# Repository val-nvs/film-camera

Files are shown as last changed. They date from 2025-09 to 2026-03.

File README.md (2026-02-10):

# 3D Printed Clawless 35mm Film Camera

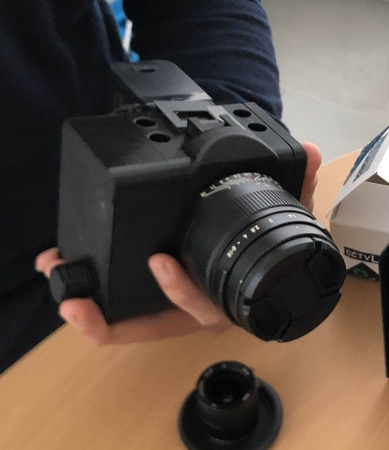
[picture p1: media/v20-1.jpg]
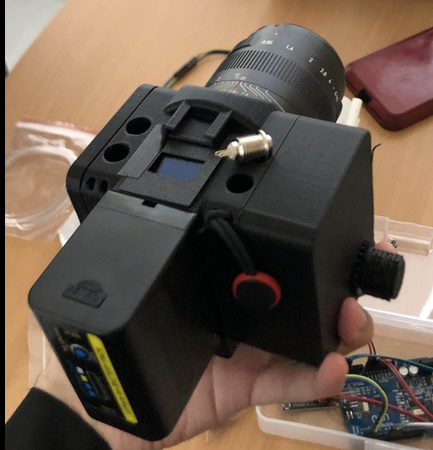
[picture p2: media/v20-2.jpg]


This repository documents the build of a 3D printed film camera that is designed to use standard 35mm 36exp film cartridges. With the goal of shooting small clips on a budget. By **[Valdir Neves](https://www.instagram.com/val.nevs/)** & **[Charlie Chaves](https://www.instagram.com/charliechavess/)**.

[{{{ **View in 3D on onshape** }}}](https://cad.onshape.com/documents/5c2b9c47264034ac5c1a5ddc/w/cf712b211e6f3dfb560adac5/e/ec23c9e4d3ee5216bc6ef26c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)

## Acknowledgements

Thanks to **[Hans Boden](https://github.com/hans-boden)** for guidance and support throughout this project, including lending a 3D printer.

Thanks to [MILL - Makers In Little Lisbon](https://www.instagram.com/lxmill/) for providing a platform for connecting with other makers.

Thanks to [Elly T.](https://www.instagram.com/forfutureelly/) and [Daniel @photonbit](https://www.instagram.com/photonbit/) for design advice.

## Inspiration

- Joshua Bird https://joshuabird.com/blog/post/3d-printed-film-video-camera
	
	
- Blaž Semprimožnik https://blazsemprimoznik.com/okto35-mk3
	
	
- Brian's Lucky Box Camera
	
	
- henry kidman
	
	
	

## About:

3D printed film camera, designed to use standard 35mm 36exp film. Capable of taking photos and making 1 to 4 short clips per roll.

Goals:

- To be a low cost-of-entry into analog motion picture with easily accesible film and labs. ~11€ film + ~15€ developing. (Super 8 starts at 23€+ B&W, color at 50€+, and it's harder to find somewhere to develop).

- To be low cost when bulk loading (when someone rolls their own 5ft rolls from a 100ft or 400ft spool). I'm using Lucky SHD50 B&W bulk loaded- 1.9€ per roll. Fomapan would be around 2.7€ per roll when bulk loaded.

Highlights:

- 2 Motors: Instead of a single motor with a system of gears to connect the shutter and pulldown mechanism, the mechanisms are independent of each other by using a motor for each.

- Clawless: Instead of claws to pulldown the film by the perforations, it simply winds the film into the camera with sticky tape. Possible due to the short total lenght of the film strip (150cm instead of 30m or 120m). Pros: simpler; frame can be any height/aspect ratio. Downside: almost impossible to project videos- must be scanned digitally.

- Multitrack video-recording: Possible to record up to 4 separate discrete tracks of video (not simultaneously) by shifting the internal assembly (and rewinding) after finishing each track. Comes with 4 options of gates to record between 1 to 4 tracks, with more options for taller aspect ratios like 1:1.

- Maximum FPS for video: ???

- Records 1600 frames per canister with the smallest gate (divided into 4 passes) (2min@13fps). Or 820 frames using a "Super 16" sized gate (divided into 2 passes), at 24fps it would be 34s of total recording time- 45s@18fps 1min@14fps.

Features:

- E-mount used, easy to adapt to many lenses And it's easier to print compared to C-mount- with it's fine threads.

- With the smallest "Super 8" gate you can film up to 1200 frames per cartridge (divided into 4 passes).

Future plans:

- OLED screen tracks how much film you used.
- Unique manual variable FPS feature designed to [save on film] or [add slow motion] mid-shoot. (Each frame will be logged in time making it easy to sync frames and sound).

## 3D model
[{{{ **View in 3D on onshape** }}}](https://cad.onshape.com/documents/5c2b9c47264034ac5c1a5ddc/w/cf712b211e6f3dfb560adac5/e/ec23c9e4d3ee5216bc6ef26c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)

## Code
[Wokwi](https://wokwi.com/projects/455248968650449921)

## Setup

- Onshape CAD software on Chrome
- UltiMaker Cura 5.11.0 Slicer
- Anycubic i3 Mega S Printer / 0.4mm nozzle / SMARTFIL 1.75mm Black PLA

## Parts

Motors:

- 1x Nema 8 Stepper Motor for the shutter 
- 1x Nema 14 Stepper Motor to pull film 

Other parts:

- 2x Stepper Driver DRV8825 
- Arduino and breadboard ~15€
- 2x Tripod threaded insert (1/4") length 6mm 
- Optional: 8x 5x3mm round magnets 
- 4x Buttons: 

Viewfinder:

- Acrylic lens 24.8mm diameter 
- Front surface mirror 30x30x2mm 
- Plastic Fresnel lens f=28mm 30x30mm 

Lens:

- Lens mount adaptor C-NEX (to support C-mount lenses) 
- Lens: 3.6-10mm f/1.4 C-Mount [1/1.8"] "8MP IR CCTV" (effectively f/2) 
- Optional: Imaging lens cover 

## 3D Printed parts (v21)

- Body
- Core
- Left and right wall
- Shutter disc
- Rewinder pin
- Optional: 2 gears and 2 locking pins

## History

Feb 10 - test failed, not enough force to pull film consistently

Feb 9 - test failed, solder fail

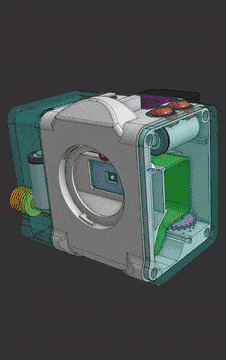
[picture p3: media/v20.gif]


v21 - TBA
```
- smaller body, eletronics outside
- integrated viewfinder into body
```

v20b - Jan 19, 2026
```
- shave off parts of gate and oled lid
- added lock pin
- supressed NPF wiring ducts
- fix shutter piece
- fix roller size
- rotate mount slightly
- widen button holes
```
v20a - Jan 9, 2026
```
- added support for roller on core
```
v20 - Jan 1, 2026
```
- FDM focused redesign
- better gears
- add 4 magnets on each wall
```

v19 - Nov 25, 2025
```
v19a: added switches - Nov 26, 2025
```
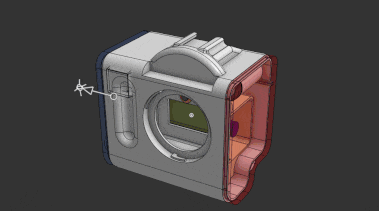
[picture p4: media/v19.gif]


v18
```
- Not symmetric
- Custom buttons
```

v17

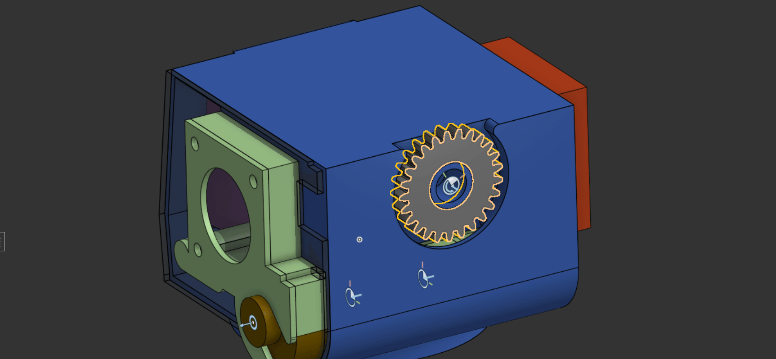
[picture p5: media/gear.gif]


```
- Gear to move core
- 2x RCR123A
- OLED
```

v16
```
- Protuding shutter design thing
```

v15
```
- Fixed wrong flange value!
- Core completely encased to prevent light leaks
- Core on bottom
- Nema 8 for film
- Nema 14 for shutter
- Cold Shoe
```

v14
```
- Nema 8 for film
- 0530 6V Solenoid for shutter
- 2x RCR123A
```

v13
```
- Tests with solenoid for shutter and shifted reel motor
```

v12 - PRINTED @JLC3DP - July 31, 2025

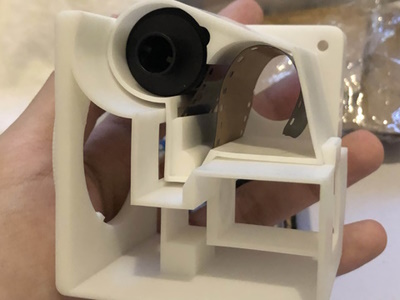
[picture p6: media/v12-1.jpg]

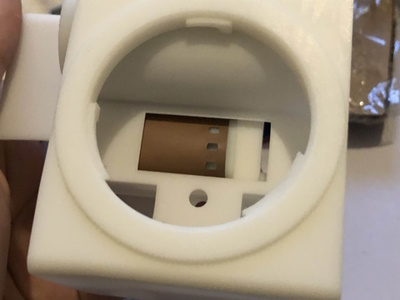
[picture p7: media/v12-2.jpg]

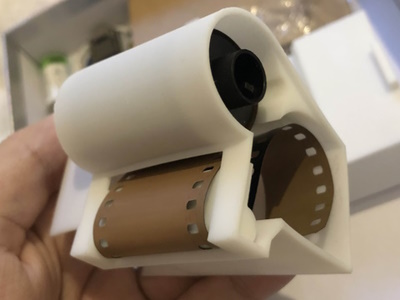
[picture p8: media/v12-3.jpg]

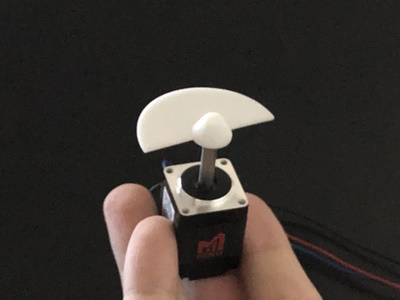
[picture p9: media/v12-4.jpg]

```
- Wrong flange value!
- Nema 14 for film 
- Nema 8 for shutter
- 71x72x67mm
- 2x RCR123A batteries and holder https://www.takachi-enclosure.com/assets/attachments/images/CR123A-PC.pdf
```


v11
```
- 4x RCR123A batteries
```

v10
```
?
```

v9


```
- Uses separate motors for each function instead of complex gears. One motor spins the shutter disc, another advances the film.
- Nema 17 for film and shutter
- 4x AAAA batteries
```

# Film scanner
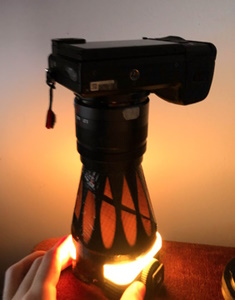
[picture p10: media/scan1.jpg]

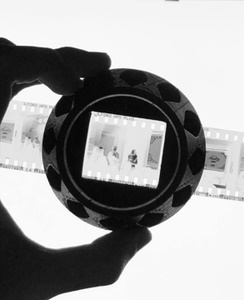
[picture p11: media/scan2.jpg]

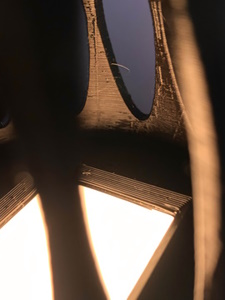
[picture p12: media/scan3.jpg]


to photo scam 35mm 8 perforations film
using 7artisans 35mm f/.95 and a small video light (NEEWER RGB61 iirc)

- v3 printed but film gets jammed
- v6 works great, 2 identical pieces that connect each-other for the base, and one tube piece to hold the lens. easy to adapt other lenses with .step file
- v7 will add phone holder to use the flashlight to see dust particles on top of the film like the laser dyson vacuum

# etc

```
38exp = 1444mm
100ft = 30480mm
24.9 width
16:9 ratio
0.05 gaps between
@ 24 fps
```

```
@ 2 columns (12.42x6.989) (86.8mm²) (7.039mm pitch)
 38 exp: 17 sec
 100 ft: 6    min
 400 ft: 24   min
1000 ft: 60.1 min
```

```
@ 3 columns (8.26x4.65) (38.4mm²) (4.700mm pitch)
- ` 38 exp`: 38.4 sec
- ` 100 ft`: 13.5  min
- ` 400 ft`: 54    min
- `1000 ft`: 135.1 min
```

```
@ 4 columns (6.187x3.48) (21.5mm²) (3.530mm pitch)
-  38 exp: 68.1 sec
-  100 ft: 23.98 min
-  400 ft: 95.92 min
- 1000 ft: 239.8 min
```

```
- Super 16 @ 16:9 crop = 88.22 mm²
- 16mm     @ 16:9 crop = 59.24 mm²
- Super 8  @ 16:9 crop = 18.87 mm²
- 8mm      @ 16:9 crop = 11.39 mm²
```

# etc
Tripod threaded insert (1/4") length 6mm

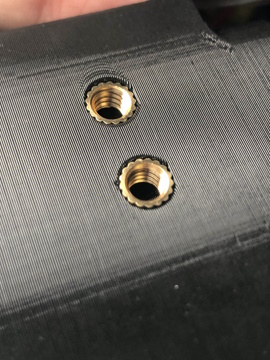
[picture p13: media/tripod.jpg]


100ft of film makes 20 "36exp" cartridges

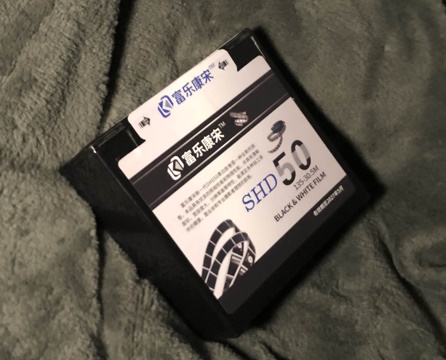
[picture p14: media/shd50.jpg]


6.3-10mm f/1.4 C-mount lens

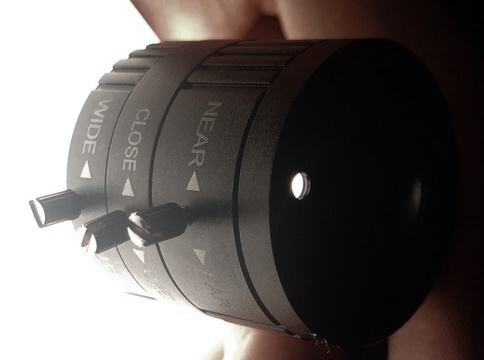
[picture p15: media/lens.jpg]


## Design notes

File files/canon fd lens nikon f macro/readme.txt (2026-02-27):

size of piece =/= macro size, due to flange difference.
macro cant go lower than around 16.5mm, due to flange difference.

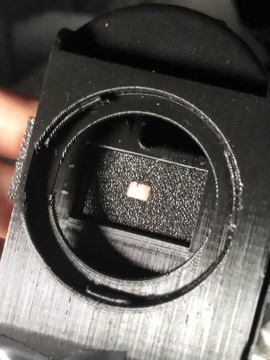
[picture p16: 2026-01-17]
media/gate.jpg

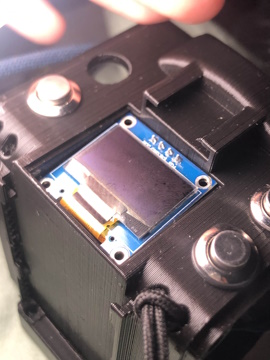
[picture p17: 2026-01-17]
media/v20-3.jpg

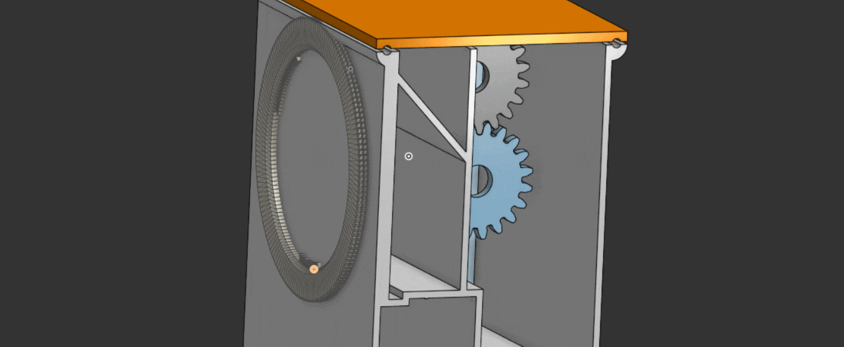
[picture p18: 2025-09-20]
media/v13.gif

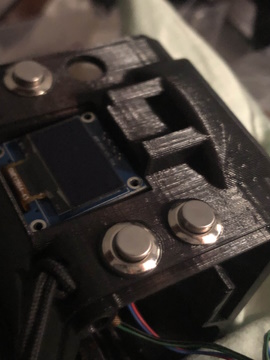
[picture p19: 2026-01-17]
media/v20-4.jpg

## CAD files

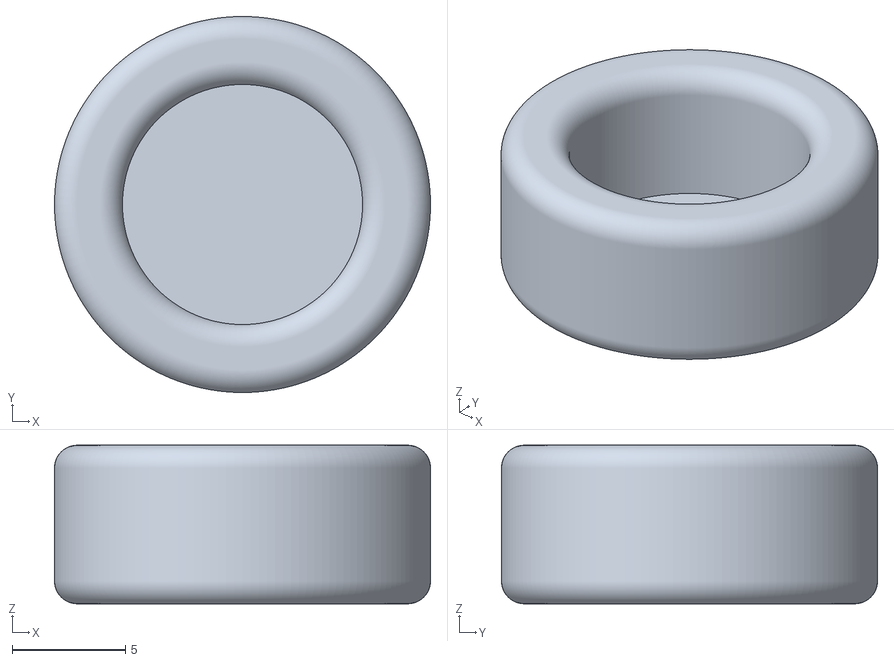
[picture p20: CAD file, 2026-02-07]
files/c-rear-element-cap.stl
16.6 x 16.6 x 7.00

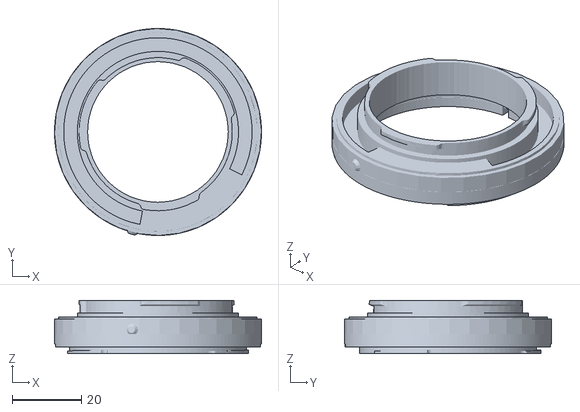
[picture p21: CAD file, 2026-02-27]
files/canon fd lens nikon f macro/FD-Lens on Nikon-F macro 20mm.stl
60.0 x 60.0 x 15.5

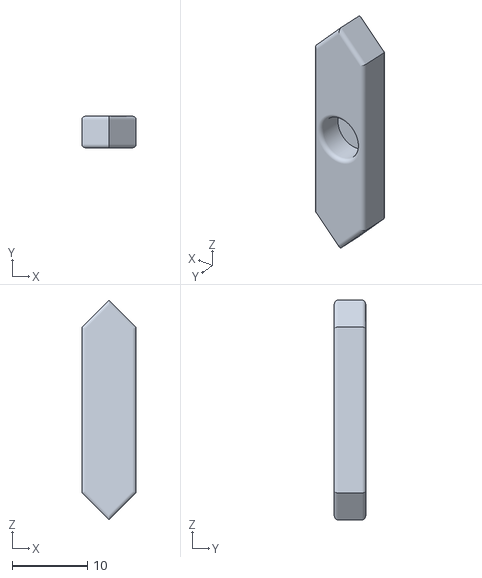
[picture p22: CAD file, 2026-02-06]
files/clapper/clapper v1/clapper v1 - segment x30.stl
7.20 x 4.20 x 29.2

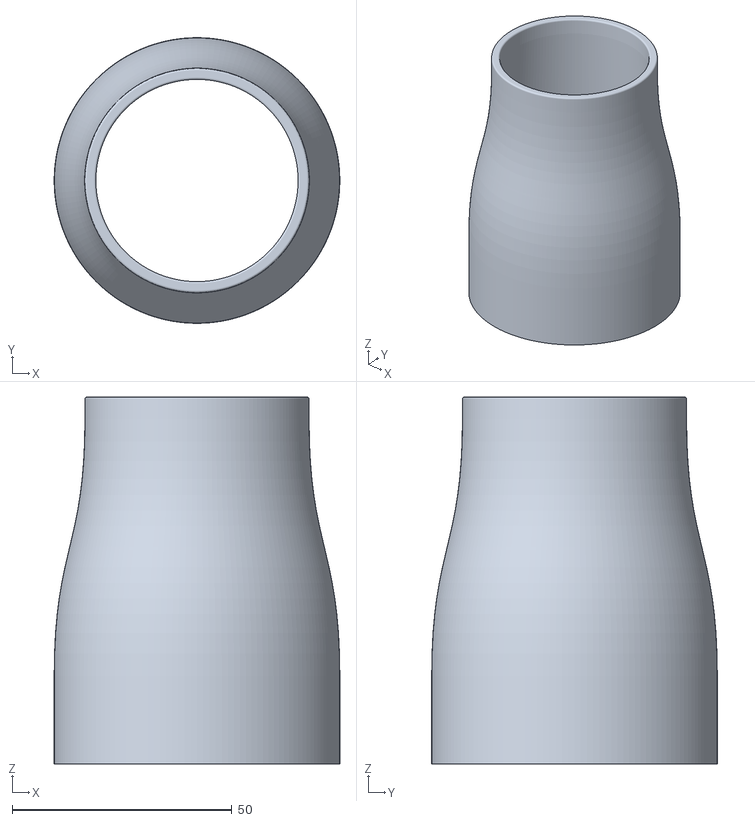
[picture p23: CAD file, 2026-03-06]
files/film scanner/scan v7/new/scan v7 test 2 - tube 90mm.stl
65.0 x 65.0 x 83.5

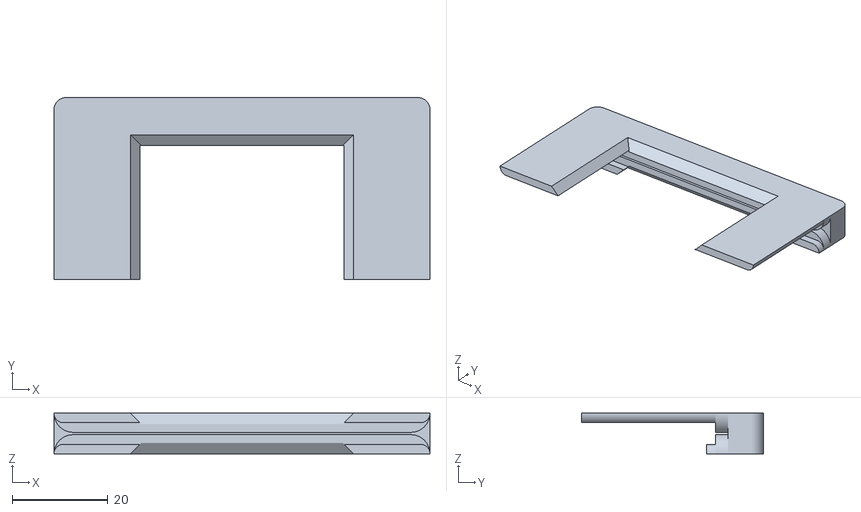
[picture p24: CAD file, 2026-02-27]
files/film scanner/scan v7/scan v7 - holder x2.stl
78.4 x 37.9 x 8.50

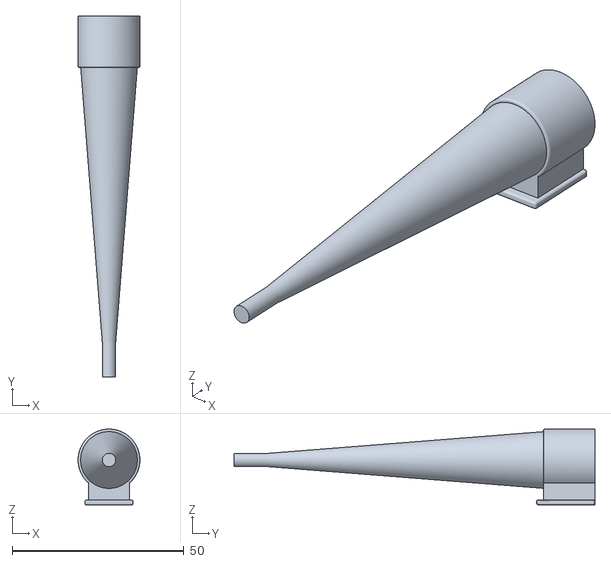
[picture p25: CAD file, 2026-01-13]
files/filter spin/filter spin 72mm - Part 3.stl
18.0 x 105.0 x 22.1

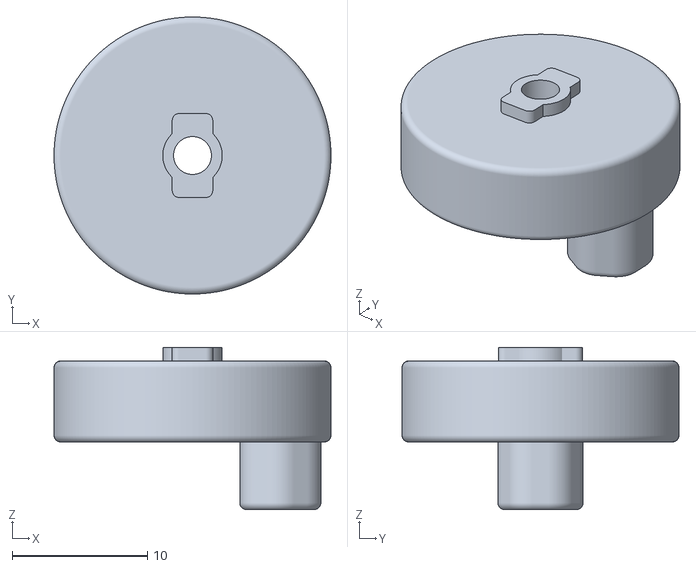
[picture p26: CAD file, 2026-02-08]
files/p30t rewinder/p30t rewinder - v2.stl
20.5 x 20.5 x 12.0

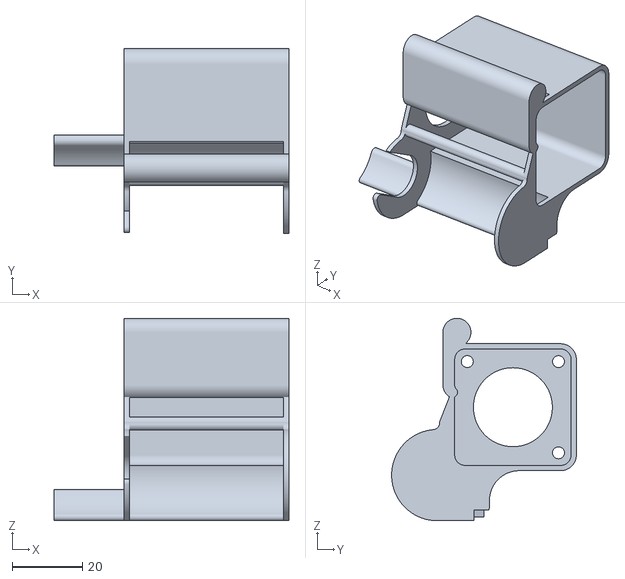
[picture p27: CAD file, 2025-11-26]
files/v19a/v19a - core.stl
67.0 x 52.7 x 57.7

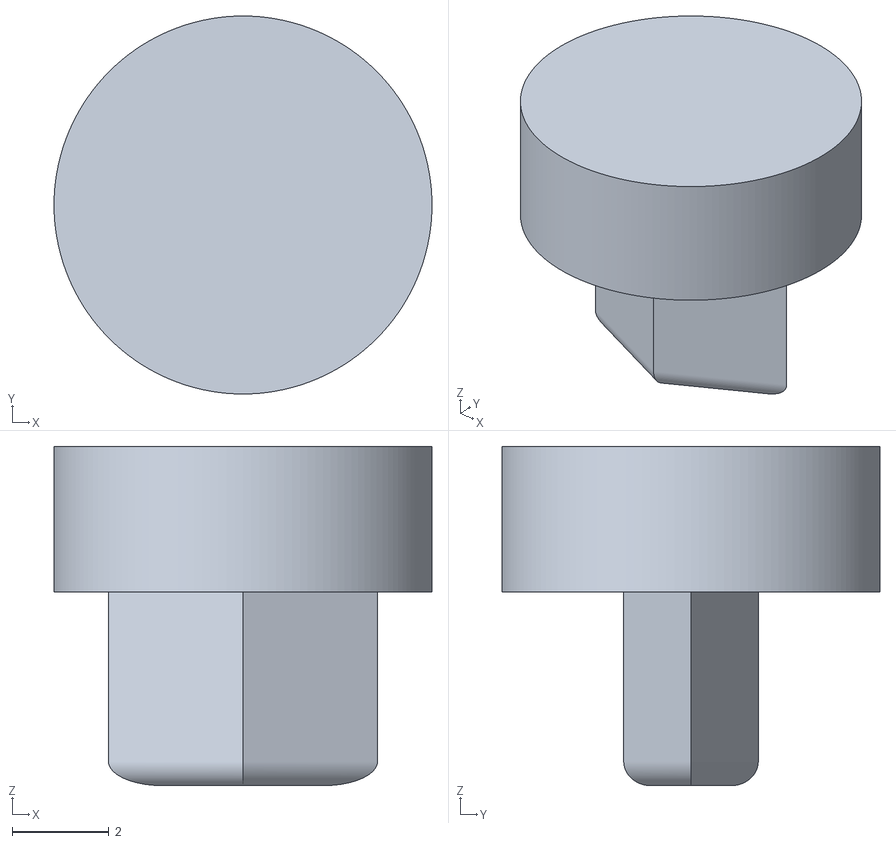
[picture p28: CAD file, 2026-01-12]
files/v20a/v20a - gear pin x3 new.stl
7.80 x 7.80 x 7.00

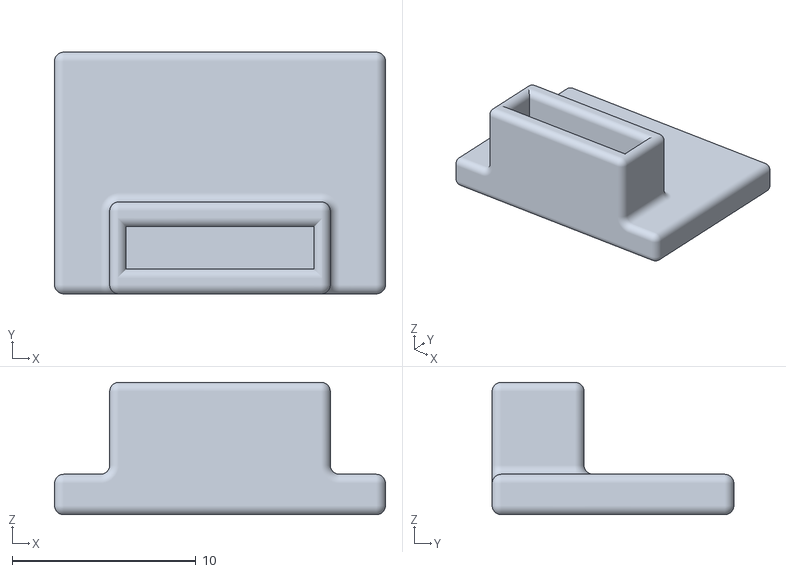
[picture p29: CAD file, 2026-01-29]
files/v20b/v20b - viewfinder part B.stl
18.0 x 13.1 x 7.20

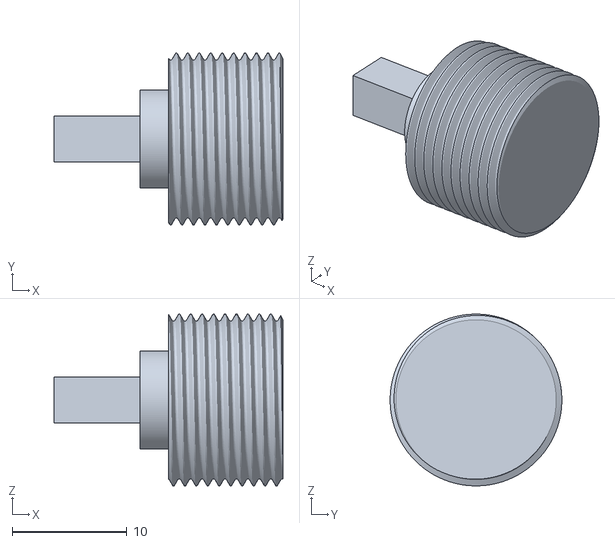
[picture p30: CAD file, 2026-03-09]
files/v24/v24 - worm knob.stl
20.0 x 15.0 x 15.0

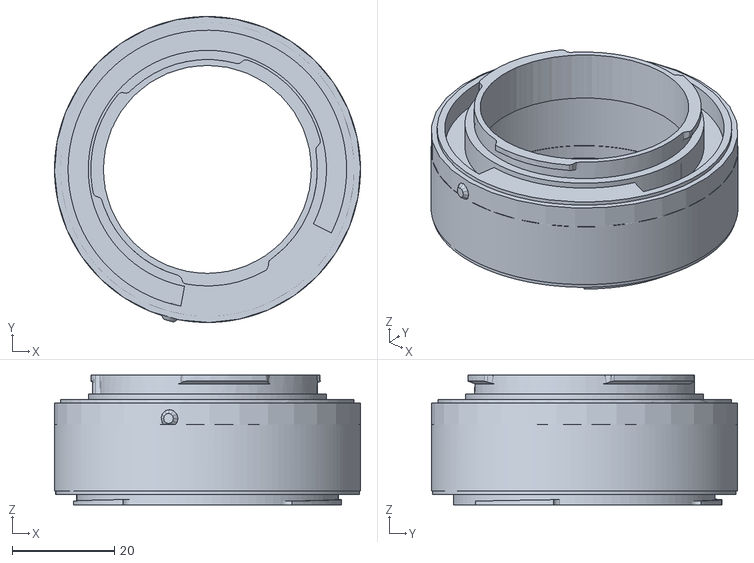
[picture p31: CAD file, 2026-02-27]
files/canon fd lens nikon f macro/FD-Lens on Nikon-F macro 30mm.stl
60.0 x 60.0 x 25.5

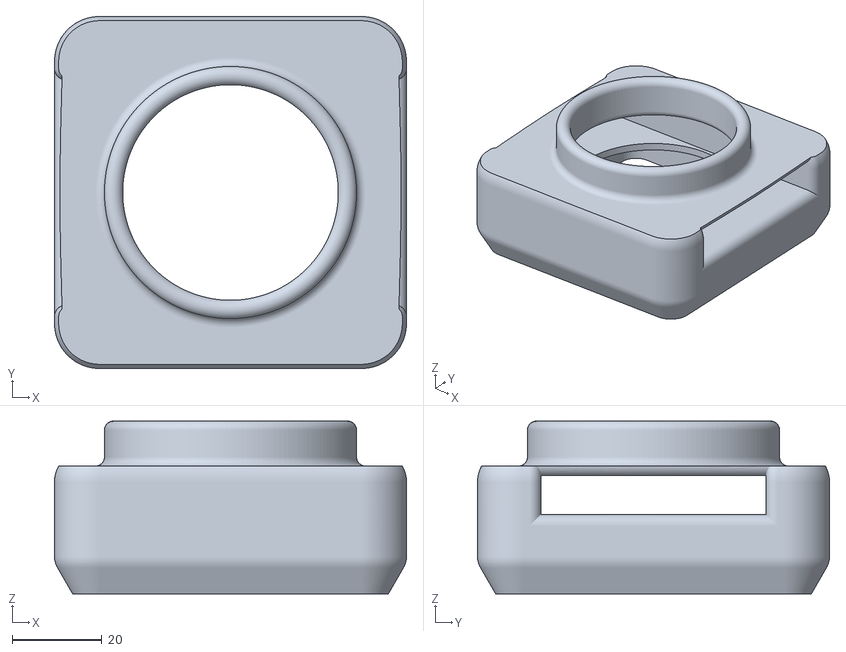
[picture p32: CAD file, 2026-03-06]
files/film scanner/scan v7/new/scan v7 test 2 - base.stl
78.4 x 78.4 x 38.5

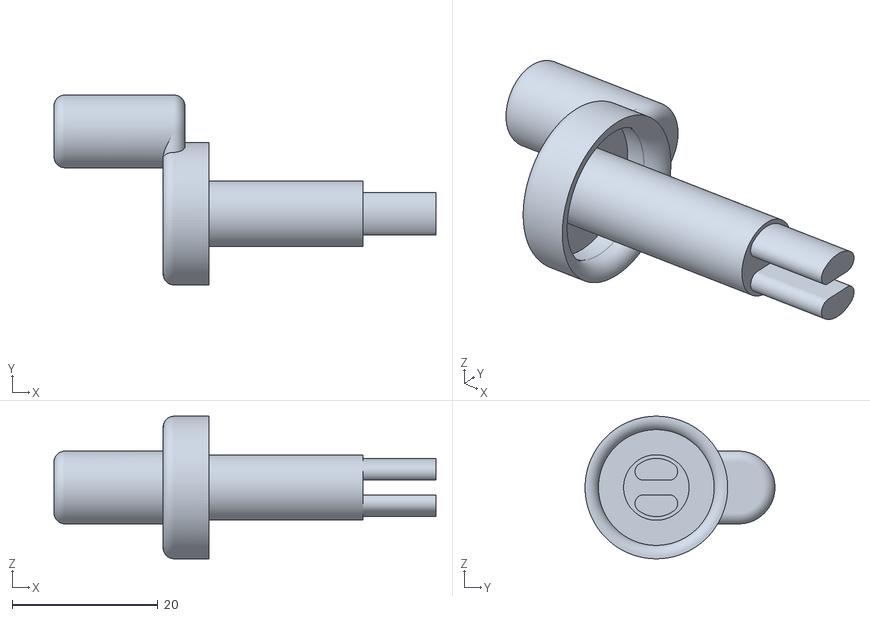
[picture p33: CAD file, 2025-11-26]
files/v19a/v19a - rewinder.stl
52.5 x 26.1 x 19.6

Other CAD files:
files/v20a/v20a - gear pin x3.stl
files/v20b/v20b - shutter.stl
files/v24/v24 - wall right.stl
files/canon fd lens nikon f macro/FD-Lens on Nikon-F macro 17mm.stl
files/canon fd lens nikon f macro/FD-Lens on Nikon-F macro 25mm.stl
files/film scanner/scan v1/scan v1 test.stl
files/film scanner/scan v1/scan v1.stl
files/film scanner/scan v2/scan v2.stl
files/film scanner/scan v3/scan v3.stl
files/film scanner/scan v4/scan v4 - base x2.stl
files/film scanner/scan v4/scan v4 - tube.stl
files/film scanner/scan v6/scan v6 - tube for 7artisans35mmf095+macro16mm.stl
files/film scanner/scan v7/new/scan v7 test 2 - base (1).stl
files/p30t rewinder/p30t rewinder - v1.stl
files/v12/v12 - core.stl
files/v12/v12 - gate 1250x700.stl
files/v12/v12 - gate 625x352.stl
files/v12/v12 - gate 833x469.stl
files/v12/v12 - lid.stl
files/v12/v12 - shutter.stl
files/v12/v12 - spool flat.stl
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

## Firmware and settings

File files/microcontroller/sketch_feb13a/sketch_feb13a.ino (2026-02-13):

#include <LedControl.h>

// ===== ARDUINO R4 WIFI BUILT-IN MATRIX - START =====
#include "Arduino_LED_Matrix.h"
// ===== ARDUINO R4 WIFI BUILT-IN MATRIX - END =====

// MAX7219 Pins: DIN=12, CLK=13, CS=A0
LedControl lc = LedControl(12, 13, A0, 2);  // 2 displays chained

// ===== ARDUINO R4 WIFI BUILT-IN MATRIX - START =====
// Built-in R4 WiFi LED Matrix
ArduinoLEDMatrix matrix;
// ===== ARDUINO R4 WIFI BUILT-IN MATRIX - END =====

// Motor Pins
const int en1 = 2, step1 = 3, dir1 = 4;
const int en2 = 5, step2 = 6, dir2 = 7;

// D-pad Buttons
const int btnDown = 8;
const int btnRight = 9;
const int btnUp = 10;
const int btnLeft = 11;

// Menu state
int currentMenu = 0;  // 0 = main menu, 1 = submenu shutter, 2 = submenu claw, 3 = shutter speed submenu, 4 = both submenu, 5 = fps submenu, 6 = duration submenu
int selectedLine = 0; // 0 = top line (motor1), 1 = middle line (motor2), 2 = bottom line (both)
int shutterSubSelection = 0; // 0 = lock, 1 = run shutter, 2 = speed settings, 3 = unused
int clawSubSelection = 0; // 0 = lock, 1 = run claw, 2 = skip, 3 = unused
int bothSubSelection = 0; // 0 = lock/unlock both, 1 = run, 2 = fps, 3 = duration
bool motor1Locked = false; // Motor 1 (shutter) lock state
bool motor2Locked = false; // Motor 2 (claw) lock state

// FPS settings for Both menu
const float fpsValues[] = {60.0, 48.0, 30.0, 24.0, 20.0, 18.0, 15.0, 12.0, 10.0, 9.0, 8.0, 6.0, 5.0, 4.0, 3.0, 2.0, 1.5}; // Frames per second
const int numFPS = 17;
int fpsIndex = 12; // Default to 5 FPS

// Duration (cycles) settings for Both menu
const int cyclesValues[] = {1, 5, 10, 20}; // Number of cycles
const int numCycles = 4;
int cyclesIndex = 0; // Default to 1 cycle

// Shutter speed array in microseconds: .1 .15 .2 .3 .4 .5 1 2 3 4 5 8 10 16 25 32 50 60 120 180
const long speedValues[] = {
  100000,    // .1
  150000,    // .15
  200000,    // .2
  300000,    // .3
  400000,    // .4
  500000,    // .5
  1000000,   // 1
  2000000,   // 2
  3000000,   // 3
  4000000,   // 4
  5000000,   // 5
  8000000,   // 8
  10000000,  // 10
  16000000,  // 16
  25000000,  // 25
  32000000,  // 32
  50000000,  // 50
  60000000,  // 60
  120000000, // 120
  180000000  // 180
};
const int numSpeeds = 20;
int speedIndex = 5; // Default to .5s (index 5)

unsigned long lastBlink = 0;
bool blinkState = false;

uint8_t frame[8][12] = {0};  // Only using 12x8 space

void setup() {
  // ===== ARDUINO R4 WIFI BUILT-IN MATRIX - START =====
  // Initialize built-in R4 WiFi LED matrix
  matrix.begin();
  // ===== ARDUINO R4 WIFI BUILT-IN MATRIX - END =====
  
  // Initialize both MAX7219 displays
  delay(50);  // Small delay before init
  lc.shutdown(0, false);  // Wake up display 0
  lc.shutdown(1, false);  // Wake up display 1
  lc.setIntensity(0, 8);  // Set brightness (0-15)
  lc.setIntensity(1, 8);
  lc.clearDisplay(0);
  lc.clearDisplay(1);
  delay(50);  // Small delay after init
  
  int outputs[] = {en1, step1, dir1, en2, step2, dir2};
  for(int p : outputs) pinMode(p, OUTPUT);
  
  int inputs[] = {btnDown, btnRight, btnUp, btnLeft};
  for(int p : inputs) pinMode(p, INPUT_PULLUP);

  digitalWrite(en1, LOW);
  digitalWrite(en2, LOW);
}

void loop() {
  handleInput();
  drawUI();
  delay(50);
}

void handleInput() {
  static bool lastBtnDown = true;
  static bool lastBtnRight = true;
  static bool lastBtnUp = true;
  static bool lastBtnLeft = true;
  
  bool currentDown = digitalRead(btnDown) == LOW;
  bool currentRight = digitalRead(btnRight) == LOW;
  bool currentUp = digitalRead(btnUp) == LOW;
  bool currentLeft = digitalRead(btnLeft) == LOW;
  
  // Main menu navigation
  if (currentMenu == 0) {
    // Down button - navigate down in main menu
    if (currentDown && !lastBtnDown) {
      if (selectedLine < 2) {
        selectedLine++;
      }
      delay(50);
    }
    
    // Up button - navigate up in main menu
    if (currentUp && !lastBtnUp) {
      if (selectedLine > 0) {
        selectedLine--;
      }
      delay(50);
    }
    
    // Right button - enter submenu
    if (currentRight && !lastBtnRight) {
      if (selectedLine == 0) {
        currentMenu = 1; // Enter shutter submenu
        shutterSubSelection = 0;
      } else if (selectedLine == 1) {
        currentMenu = 2; // Enter claw submenu
        clawSubSelection = 0;
      } else {
        currentMenu = 4; // Enter both submenu
        bothSubSelection = 0;
      }
      delay(200); // Longer delay to prevent immediate activation in submenu
    }
  }
  // Shutter submenu
  else if (currentMenu == 1) {
    // Left button - go back to main menu
    if (currentLeft && !lastBtnLeft) {
      currentMenu = 0;
      delay(50);
    }
    
    // Down button - navigate down
    if (currentDown && !lastBtnDown) {
      if (shutterSubSelection < 3) {
        shutterSubSelection++;
      }
      delay(50);
    }
    
    // Up button - navigate up
    if (currentUp && !lastBtnUp) {
      if (shutterSubSelection > 0) {
        shutterSubSelection--;
      }
      delay(50);
    }
    
    // Right button - enter action or submenu
    if (currentRight && !lastBtnRight) {
      if (shutterSubSelection == 0) {
        // Toggle lock
        motor1Locked = !motor1Locked;
        digitalWrite(en1, motor1Locked ? HIGH : LOW);
      } else if (shutterSubSelection == 1) {
        // Run shutter motor 200 steps
        runMotor(en1, step1, dir1, 200, speedValues[speedIndex]);
      } else if (shutterSubSelection == 2) {
        // Enter speed settings submenu
        currentMenu = 3;
      }
      // Option 3 does nothing
      delay(200); // Longer delay to prevent immediate activation
    }
  }
  // Claw submenu
  else if (currentMenu == 2) {
    // Left button - go back to main menu
    if (currentLeft && !lastBtnLeft) {
      currentMenu = 0;
      delay(50);
    }
    
    // Down button - navigate down
    if (currentDown && !lastBtnDown) {
      if (clawSubSelection < 3) {
        clawSubSelection++;
      }
      delay(50);
    }
    
    // Up button - navigate up
    if (currentUp && !lastBtnUp) {
      if (clawSubSelection > 0) {
        clawSubSelection--;
      }
      delay(50);
    }
    
    // Right button - action
    if (currentRight && !lastBtnRight) {
      if (clawSubSelection == 0) {
        // Toggle lock
        motor2Locked = !motor2Locked;
        digitalWrite(en2, motor2Locked ? HIGH : LOW);
      } else if (clawSubSelection == 1) {
        // Run claw motor (MOTOR 2!) - 200 steps, 200ms total (1000μs per pulse)
        runMotor(en2, step2, dir2, 200, 200000);
      } else if (clawSubSelection == 2) {
        // Skip - Run claw motor 10x (2000 steps, 2000ms total)
        runMotor(en2, step2, dir2, 2000, 2000000);
      }
      // Option 3 does nothing
      delay(200);
    }
  }
  // Shutter speed settings submenu
  else if (currentMenu == 3) {
    // Left button - go back to shutter submenu
    if (currentLeft && !lastBtnLeft) {
      currentMenu = 1;
      delay(200);
    }
    
    // Up button - increase time (slower shutter)
    if (currentUp && !lastBtnUp) {
      if (speedIndex < numSpeeds - 1) {
        speedIndex++;
      }
      delay(200);
    }
    
    // Down button - decrease time (faster shutter)
    if (currentDown && !lastBtnDown) {
      if (speedIndex > 0) {
        speedIndex--;
      }
      delay(200);
    }
  }
  // Both submenu
  else if (currentMenu == 4) {
    // Left button - go back to main menu
    if (currentLeft && !lastBtnLeft) {
      currentMenu = 0;
      delay(50);
    }
    
    // Down button - navigate down
    if (currentDown && !lastBtnDown) {
      if (bothSubSelection < 3) {
        bothSubSelection++;
      }
      delay(50);
    }
    
    // Up button - navigate up
    if (currentUp && !lastBtnUp) {
      if (bothSubSelection > 0) {
        bothSubSelection--;
      }
      delay(50);
    }
    
    // Right button - enter action or submenu
    if (currentRight && !lastBtnRight) {
      if (bothSubSelection == 0) {
        // Lock/Unlock both motors
        // If both are locked, unlock both
        // If only one or none are locked, lock both
        if (motor1Locked && motor2Locked) {
          // Unlock both
          motor1Locked = false;
          motor2Locked = false;
          digitalWrite(en1, LOW);
          digitalWrite(en2, LOW);
        } else {
          // Lock both
          motor1Locked = true;
          motor2Locked = true;
          digitalWrite(en1, HIGH);
          digitalWrite(en2, HIGH);
        }
      } else if (bothSubSelection == 1) {
        // Run both motors for selected cycles
        runBothCycle();
      } else if (bothSubSelection == 2) {
        // Enter FPS settings submenu
        currentMenu = 5;
      } else if (bothSubSelection == 3) {
        // Enter Duration settings submenu
        currentMenu = 6;
      }
      delay(200);
    }
  }
  // FPS settings submenu
  else if (currentMenu == 5) {
    // Left button - go back to both submenu
    if (currentLeft && !lastBtnLeft) {
      currentMenu = 4;
      delay(200);
    }
    
    // Up button - increase FPS (faster)
    if (currentUp && !lastBtnUp) {
      if (fpsIndex > 0) {
        fpsIndex--;
      }
      delay(200);
    }
    
    // Down button - decrease FPS (slower)
    if (currentDown && !lastBtnDown) {
      if (fpsIndex < numFPS - 1) {
        fpsIndex++;
      }
      delay(200);
    }
  }
  // Duration (cycles) settings submenu
  else if (currentMenu == 6) {
    // Left button - go back to both submenu
    if (currentLeft && !lastBtnLeft) {
      currentMenu = 4;
      delay(200);
    }
    
    // Up button - increase cycles
    if (currentUp && !lastBtnUp) {
      if (cyclesIndex < numCycles - 1) {
        cyclesIndex++;
      }
      delay(200);
    }
    
    // Down button - decrease cycles
    if (currentDown && !lastBtnDown) {
      if (cyclesIndex > 0) {
        cyclesIndex--;
      }
      delay(200);
    }
  }
  
  lastBtnDown = currentDown;
  lastBtnRight = currentRight;
  lastBtnUp = currentUp;
  lastBtnLeft = currentLeft;
}

void drawUI() {
  memset(frame, 0, sizeof(frame));
  
  // Handle blinking - faster rate for selected items
  if (millis() - lastBlink > 250) {
    blinkState = !blinkState;
    lastBlink = millis();
  }
  
  if (currentMenu == 0) {
    drawMainMenu();
  } else if (currentMenu == 1) {
    drawShutterMenu();
  } else if (currentMenu == 2) {
    drawClawMenu();
  } else if (currentMenu == 3) {
    drawSpeedMenu();
  } else if (currentMenu == 4) {
    drawBothMenu();
  } else if (currentMenu == 5) {
    drawFPSMenu();
  } else if (currentMenu == 6) {
    drawDurationMenu();
  }
  
  // Always show lock indicators
  // Shutter (motor1) lock at column 10, row 0
  if (motor1Locked) {
    frame[0][10] = 1;
  }
  // Claw (motor2) lock at column 11, row 0
  if (motor2Locked) {
    frame[0][11] = 1;
  }
  
  // ===== ARDUINO R4 WIFI BUILT-IN MATRIX - START =====
  // Render to built-in R4 WiFi LED matrix
  matrix.renderBitmap(frame, 8, 12);
  // ===== ARDUINO R4 WIFI BUILT-IN MATRIX - END =====
  
  // Render to MAX7219 displays - only use 12 columns
  // Display 1 (left) = columns 0-7, Display 0 (right) = columns 8-11
  for (int row = 0; row < 8; row++) {
    byte col0 = 0, col1 = 0;
    
    // Display 1 - left side (columns 0-7)
    for (int col = 0; col < 8; col++) {
      if (frame[row][col]) {
        col1 |= (1 << col);
      }
    }
    
    // Display 0 - right side (columns 8-11 only)
    for (int col = 8; col < 12; col++) {
      if (frame[row][col]) {
        col0 |= (1 << (col - 8));
      }
    }
    
    lc.setRow(0, row, col0);
    lc.setRow(1, row, col1);
  }
}

void drawMainMenu() {
  // Draw motor1 selector (top box, rows 0-1, cols 0-1)
  // Always show, blink if selected
  if (selectedLine != 0 || (selectedLine == 0 && blinkState)) {
    frame[0][0] = 1; frame[0][1] = 1;
    frame[1][0] = 1; frame[1][1] = 1;
  }
  
  // Draw motor2 selector (2nd box, rows 2-3, cols 0-1) - touching the top box
  // Always show, blink if selected
  if (selectedLine != 1 || (selectedLine == 1 && blinkState)) {
    frame[2][0] = 1; frame[2][1] = 1;
    frame[3][0] = 1; frame[3][1] = 1;
  }
  
  // Draw both selector (3rd box, rows 4-5, cols 0-1) - selectable
  if (selectedLine != 2 || (selectedLine == 2 && blinkState)) {
    frame[4][0] = 1; frame[4][1] = 1;
    frame[5][0] = 1; frame[5][1] = 1;
  }
  
  // Draw 4th box (rows 6-7, cols 0-1) - useless for now, always solid
  frame[6][0] = 1; frame[6][1] = 1;
  frame[7][0] = 1; frame[7][1] = 1;
  
  // Draw rolling text starting at column 3
  if (selectedLine == 0) {
    drawRollingText("Shutter", 3);
  } else if (selectedLine == 1) {
    drawRollingText("Claw", 3);
  } else {
    drawRollingText("Both", 3);
  }
}

void drawRollingText(const char* text, int startCol) {
  static unsigned long lastScroll = 0;
  static int scrollOffset = 0;
  static int lastMenu = -1;
  static int lastSelection = -1;
  
  // Reset scroll when menu or selection changes
  int currentSelection = (currentMenu == 0) ? selectedLine : 
                        (currentMenu == 1) ? shutterSubSelection : 
                        (currentMenu == 2) ? clawSubSelection : 
                        (currentMenu == 4) ? bothSubSelection :
                        (currentMenu == 5) ? fpsIndex :
                        (currentMenu == 6) ? cyclesIndex : 0;
  
  if (currentMenu != lastMenu || currentSelection != lastSelection) {
    scrollOffset = 0;
    lastMenu = currentMenu;
    lastSelection = currentSelection;
    lastScroll = millis(); // Reset timer too
  }
  
  // Update scroll position every 100ms
  if (millis() - lastScroll > 100) {
    scrollOffset++;
    lastScroll = millis();
  }
  
  // Calculate total text width with variable spacing
  int totalWidth = 0;
  int textLen = strlen(text);
  for (int i = 0; i < textLen; i++) {
    totalWidth += getCharWidth(text[i]) + 1; // char width + 1px gap
  }
  
  // Reset scroll when text completely scrolled off the left side
  if (scrollOffset >= totalWidth + 12) {
    scrollOffset = 0;
  }
  
  // Draw each character with variable spacing
  int currentX = 12 - scrollOffset;
  for (int i = 0; i < textLen; i++) {
    int charWidth = getCharWidth(text[i]);
    
    // Only draw if character is visible on screen (between startCol and 12)
    if (currentX + charWidth > startCol && currentX < 12) {
      drawChar(text[i], currentX, 0);
    }
    
    currentX += charWidth + 1; // Move by char width + 1px gap
  }
}

int getCharWidth(char c) {
  // Return the actual pixel width of each character (rightmost - leftmost + 1)
  switch(c) {
    case 'S': return 5;
    case 'h': return 5;
    case 'u': return 5;
    case 't': return 3;
    case 'e': return 5;
    case 'r': return 5;
    case 'C': return 5;
    case 'l': return 2;
    case 'a': return 5;
    case 'w': return 5;
    case 'L': return 5;
    case 'o': return 5;
    case 'c': return 5;
    case 'k': return 4;
    case 'U': return 5;
    case 'n': return 5;
    case 'R': return 5;
    case 'T': return 5;
    case 'i': return 1;
    case 'm': return 5;
    case 'p': return 5;
    case 'B': return 5;
    case 'F': return 5;
    case 'P': return 5;
    case 'D': return 5;
    default: return 3; // Default for unknown chars
  }
}

void drawChar(char c, int x, int y) {
  // Simple variable-width font patterns (7 pixels tall)
  byte charData[7];
  
  switch(c) {
    case 'S':
      charData[0] = 0b01111;
      charData[1] = 0b10000;
      charData[2] = 0b01110;
      charData[3] = 0b00001;
      charData[4] = 0b00001;
      charData[5] = 0b10001;
      charData[6] = 0b01110;
      break;
    case 'h':
      charData[0] = 0b10000;
      charData[1] = 0b10000;
      charData[2] = 0b10110;
      charData[3] = 0b11001;
      charData[4] = 0b10001;
      charData[5] = 0b10001;
      charData[6] = 0b10001;
      break;
    case 'u':
      charData[0] = 0b00000;
      charData[1] = 0b00000;
      charData[2] = 0b10001;
      charData[3] = 0b10001;
      charData[4] = 0b10001;
      charData[5] = 0b10001;
      charData[6] = 0b01111;
      break;
    case 't':
      charData[0] = 0b010;
      charData[1] = 0b111;
      charData[2] = 0b010;
      charData[3] = 0b010;
      charData[4] = 0b010;
      charData[5] = 0b010;
      charData[6] = 0b001;
      break;
    case 'e':
      charData[0] = 0b00000;
      charData[1] = 0b00000;
      charData[2] = 0b01110;
      charData[3] = 0b10001;
      charData[4] = 0b11111;
      charData[5] = 0b10000;
      charData[6] = 0b01111;
      break;
    case 'r':
      charData[0] = 0b00000;
      charData[1] = 0b00000;
      charData[2] = 0b10110;
      charData[3] = 0b11001;
      charData[4] = 0b10000;
      charData[5] = 0b10000;
      charData[6] = 0b10000;
      break;
    case 'C':
      charData[0] = 0b01110;
      charData[1] = 0b10001;
      charData[2] = 0b10000;
      charData[3] = 0b10000;
      charData[4] = 0b10001;
      charData[5] = 0b10001;
      charData[6] = 0b01110;
      break;
    case 'l':
      charData[0] = 0b10;
      charData[1] = 0b10;
      charData[2] = 0b10;
      charData[3] = 0b10;
      charData[4] = 0b10;
      charData[5] = 0b10;
      charData[6] = 0b01;
      break;
    case 'a':
      charData[0] = 0b00000;
      charData[1] = 0b00000;
      charData[2] = 0b01110;
      charData[3] = 0b00001;
      charData[4] = 0b01111;
      charData[5] = 0b10001;
      charData[6] = 0b01111;
      break;
    case 'w':
      charData[0] = 0b00000;
      charData[1] = 0b00000;
      charData[2] = 0b10001;
      charData[3] = 0b10001;
      charData[4] = 0b10101;
      charData[5] = 0b10101;
      charData[6] = 0b01011;
      break;
    case 'L':
      charData[0] = 0b10000;
      charData[1] = 0b10000;
      charData[2] = 0b10000;
      charData[3] = 0b10000;
      charData[4] = 0b10000;
      charData[5] = 0b10000;
      charData[6] = 0b11111;
      break;
    case 'o':
      charData[0] = 0b00000;
      charData[1] = 0b00000;
      charData[2] = 0b01110;
      charData[3] = 0b10001;
      charData[4] = 0b10001;
      charData[5] = 0b10001;
      charData[6] = 0b01110;
      break;
    case 'c':
      charData[0] = 0b00000;
      charData[1] = 0b00000;
      charData[2] = 0b01110;
      charData[3] = 0b10001;
      charData[4] = 0b10000;
      charData[5] = 0b10001;
      charData[6] = 0b01110;
      break;
    case 'k':
      charData[0] = 0b1000;
      charData[1] = 0b1000;
      charData[2] = 0b1001;
      charData[3] = 0b1010;
      charData[4] = 0b1100;
      charData[5] = 0b1010;
      charData[6] = 0b1001;
      break;
    case 'U':
      charData[0] = 0b10001;
      charData[1] = 0b10001;
      charData[2] = 0b10001;
      charData[3] = 0b10001;
      charData[4] = 0b10001;
      charData[5] = 0b10001;
      charData[6] = 0b01110;
      break;
    case 'n':
      charData[0] = 0b00000;
      charData[1] = 0b00000;
      charData[2] = 0b11110;
      charData[3] = 0b10001;
      charData[4] = 0b10001;
      charData[5] = 0b10001;
      charData[6] = 0b10001;
      break;
    case 'R':
      charData[0] = 0b11110;
      charData[1] = 0b10001;
      charData[2] = 0b11110;
      charData[3] = 0b10001;
      charData[4] = 0b10001;
      charData[5] = 0b10001;
      charData[6] = 0b10001;
      break;
    case 'T':
      charData[0] = 0b11111;
      charData[1] = 0b00100;
      charData[2] = 0b00100;
      charData[3] = 0b00100;
      charData[4] = 0b00100;
      charData[5] = 0b00100;
      charData[6] = 0b00100;
      break;
    case 'i':
      charData[0] = 0b1;
      charData[1] = 0b0;
      charData[2] = 0b1;
      charData[3] = 0b1;
      charData[4] = 0b1;
      charData[5] = 0b1;
      charData[6] = 0b1;
      break;
    case 'm':
      charData[0] = 0b00000;
      charData[1] = 0b00000;
      charData[2] = 0b11010;
      charData[3] = 0b10101;
      charData[4] = 0b10101;
      charData[5] = 0b10001;
      charData[6] = 0b10001;
      break;
    case 'p':
      charData[0] = 0b00000;
      charData[1] = 0b10110;
      charData[2] = 0b11001;
      charData[3] = 0b10001;
      charData[4] = 0b11110;
      charData[5] = 0b10000;
      charData[6] = 0b10000;
      break;
    case 'B':
      charData[0] = 0b11110;
      charData[1] = 0b10001;
      charData[2] = 0b11110;
      charData[3] = 0b10001;
      charData[4] = 0b10001;
      charData[5] = 0b10001;
      charData[6] = 0b11110;
      break;
    case 'F':
      charData[0] = 0b11111;
      charData[1] = 0b10000;
      charData[2] = 0b11110;
      charData[3] = 0b10000;
      charData[4] = 0b10000;
      charData[5] = 0b10000;
      charData[6] = 0b10000;
      break;
    case 'P':
      charData[0] = 0b11110;
      charData[1] = 0b10001;
      charData[2] = 0b10001;
      charData[3] = 0b11110;
      charData[4] = 0b10000;
      charData[5] = 0b10000;
      charData[6] = 0b10000;
      break;
    case 'D':
      charData[0] = 0b11110;
      charData[1] = 0b10001;
      charData[2] = 0b10001;
      charData[3] = 0b10001;
      charData[4] = 0b10001;
      charData[5] = 0b10001;
      charData[6] = 0b11110;
      break;
    default:
      // Space or unknown character
      for (int i = 0; i < 7; i++) charData[i] = 0;
      break;
  }
  
  // Draw the character starting at row 1 - only draw pixels that are >= column 3 and < column 12
  // Get the width of this character to determine how many columns to check
  int charWidth = getCharWidth(c);
  
  for (int row = 0; row < 7; row++) {
    for (int col = 0; col < charWidth; col++) {
      int pixelX = x + col;
      if (pixelX >= 3 && pixelX < 12) {  // Clip to start at column 3
        if (charData[row] & (1 << (charWidth - 1 - col))) {
          frame[row + 1][pixelX] = 1;  // Start at row 1 (2nd row)
        }
      }
    }
  }
}
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

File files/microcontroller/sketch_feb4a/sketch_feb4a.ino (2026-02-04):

#include "Arduino_LED_Matrix.h"

/* BUTTON LAYOUT REFERENCE:
 * 
 * IDLE MODE:
 *   Button 1 (pin 8):  Enter MOTOR 1 MODE
 *   Button 2 (pin 9):  Enter MOTOR 2 MODE
 *   Button 3 (pin 10): (unused)
 *   Button 4 (pin 11): (unused)
 * 
 * MOTOR 1 MODE:
 *   Button 1: RUN Motor 1
 *   Button 2: TOGGLE LOCK Motor 1
 *   Button 3: Enter SPEED submenu for Motor 1
 *   Button 4: BACK to IDLE
 * 
 * MOTOR 1 SPEED SUBMENU:
 *   Button 1: Speed UP for Motor 1 (cycles 0.5s→1s→2s→4s→8s→16s)
 *   Button 2: Speed DOWN for Motor 1 (cycles 16s→8s→4s→2s→1s→0.5s)
 *   Button 3: (unused)
 *   Button 4: BACK to MOTOR 1 MODE
 * 
 * MOTOR 2 MODE:
 *   Button 1: RUN Motor 2
 *   Button 2: TOGGLE LOCK Motor 2
 *   Button 3: Enter SPEED submenu for Motor 2
 *   Button 4: BACK to IDLE
 * 
 * MOTOR 2 SPEED SUBMENU:
 *   Button 1: Speed UP for Motor 2 (cycles 0.5s→1s→2s→4s→8s→16s)
 *   Button 2: Speed DOWN for Motor 2 (cycles 16s→8s→4s→2s→1s→0.5s)
 *   Button 3: (unused)
 *   Button 4: BACK to MOTOR 2 MODE
 * 
 * DISPLAY (Folder-based UI):
 *   Layout (8x12 LED matrix):
 *     Rows 0-2: Motor 1 folder (3 pixels high)
 *     Row 3:    Motor 1 speed indicator (2x1 LED pairs, 1-6 pairs)
 *     Rows 4-6: Motor 2 folder (3 pixels high)
 *     Row 7:    Motor 2 speed indicator (2x1 LED pairs, 1-6 pairs)
 *   
 *   IDLE MODE:
 *     - Both folders closed, speed indicators visible below each
 *   
 *   MOTOR MODE (folder open):
 *     - Selected folder shows "open" with 3 menu item icons:
 *       · RUN icon (play triangle, filled when active)
 *       · LOCK icon (solid when locked, outline when unlocked)
 *       · SPEED icon (bars)
 *     - Speed indicator always visible below folder
 *   
 *   SPEED SUBMENU:
 *     - Open folder with speed indicator below showing current setting
 *     - Speed shown as 2x1 LED pairs: 1 pair=0.5s, 2=1s, 3=2s, 4=4s, 5=8s, 6=16s
 */

ArduinoLEDMatrix matrix;

// Motor 1 Pins
const int en1 = 2, step1 = 3, dir1 = 4;

// Motor 2 Pins
const int en2 = 5, step2 = 6, dir2 = 7;

// Button Pins
const int btn1 = 8, btn2 = 9, btn3 = 10, btn4 = 11;

// State Machine
enum State { IDLE, MOTOR1_MODE, MOTOR1_SPEED, MOTOR2_MODE, MOTOR2_SPEED };
State currentState = IDLE;

// Motor States
bool lock1 = false;
bool lock2 = false;

// Speed Settings (each motor has its own speed)
// Speed index: 0=0.5s, 1=1s, 2=2s, 3=4s, 4=8s, 5=16s (6 total speeds)
int speedIndex1 = 1; // Motor 1 starts at 1s
int speedIndex2 = 1; // Motor 2 starts at 1s

/* SPEED CALCULATION MATH:
 * Given: 200 steps total, need timing from step 31 (55°) to step 169 (305°) = 139 steps
 * 
 * For desired duration D (in seconds):
 * - Total microseconds: D × 1,000,000
 * - Microseconds per step: (D × 1,000,000) / 139
 * - Each step has 2 phases (HIGH + LOW), so delay per phase: (D × 1,000,000) / (139 × 2)
 * 
 * Simplified: delay_microseconds = (D × 1,000,000) / 278
 * 
 * For our speeds:
 * 0.5s: (0.5 × 1,000,000) / 278 = 1,799 μs
 * 1s:   (1.0 × 1,000,000) / 278 = 3,597 μs
 * 2s:   (2.0 × 1,000,000) / 278 = 7,194 μs
 * 4s:   (4.0 × 1,000,000) / 278 = 14,388 μs
 * 8s:   (8.0 × 1,000,000) / 278 = 28,776 μs
 * 16s:  (16.0 × 1,000,000) / 278 = 57,554 μs
 */
const unsigned long speedDelays[6] = {
  1799,    // 0.5s
  3597,    // 1s
  7194,    // 2s
  14388,   // 4s
  28776,   // 8s
  57554    // 16s
};

// Display
uint8_t frame[8][12] = {0};

// Button debouncing
bool lastBtn1 = false, lastBtn2 = false, lastBtn3 = false, lastBtn4 = false;

void setup() {
  matrix.begin();
  
  // Setup motor pins
  int outputs[] = {en1, step1, dir1, en2, step2, dir2};
  for(int p : outputs) pinMode(p, OUTPUT);
  
  // Setup button pins
  int inputs[] = {btn1, btn2, btn3, btn4};
  for(int p : inputs) pinMode(p, INPUT_PULLUP);

  // Start both motors unlocked (sleep mode)
  digitalWrite(en1, LOW);
  digitalWrite(en2, LOW);
}

void loop() {
  // Read buttons with debouncing
  bool btn1Pressed = (digitalRead(btn1) == LOW) && !lastBtn1;
  bool btn2Pressed = (digitalRead(btn2) == LOW) && !lastBtn2;
  bool btn3Pressed = (digitalRead(btn3) == LOW) && !lastBtn3;
  bool btn4Pressed = (digitalRead(btn4) == LOW) && !lastBtn4;
  
  lastBtn1 = (digitalRead(btn1) == LOW);
  lastBtn2 = (digitalRead(btn2) == LOW);
  lastBtn3 = (digitalRead(btn3) == LOW);
  lastBtn4 = (digitalRead(btn4) == LOW);

  // State machine logic
  switch(currentState) {
    case IDLE:
      if (btn1Pressed) {
        currentState = MOTOR1_MODE;
      }
      else if (btn2Pressed) {
        currentState = MOTOR2_MODE;
      }
      // Button 3 unused in IDLE
      // Button 4 unused in IDLE
      break;

    case MOTOR1_MODE:
      if (btn1Pressed) {
        // RUN Motor 1
        runMotor(en1, step1, dir1, lock1, speedIndex1);
      }
      else if (btn2Pressed) {
        // TOGGLE LOCK Motor 1
        lock1 = !lock1;
        digitalWrite(en1, lock1 ? HIGH : LOW);
      }
      else if (btn3Pressed) {
        // Enter SPEED submenu for Motor 1
        currentState = MOTOR1_SPEED;
      }
      else if (btn4Pressed) {
        // BACK to IDLE
        currentState = IDLE;
      }
      break;

    case MOTOR1_SPEED:
      if (btn1Pressed) {
        // Speed UP for Motor 1
        speedIndex1 = (speedIndex1 + 1) % 6;
      }
      else if (btn2Pressed) {
        // Speed DOWN for Motor 1
        speedIndex1 = (speedIndex1 - 1 + 6) % 6;
      }
      else if (btn4Pressed) {
        // BACK to MOTOR1_MODE
        currentState = MOTOR1_MODE;
      }
      break;

    case MOTOR2_MODE:
      if (btn1Pressed) {
        // RUN Motor 2
        runMotor(en2, step2, dir2, lock2, speedIndex2);
      }
      else if (btn2Pressed) {
        // TOGGLE LOCK Motor 2
        lock2 = !lock2;
        digitalWrite(en2, lock2 ? HIGH : LOW);
      }
      else if (btn3Pressed) {
        // Enter SPEED submenu for Motor 2
        currentState = MOTOR2_SPEED;
      }
      else if (btn4Pressed) {
        // BACK to IDLE
        currentState = IDLE;
      }
      break;

    case MOTOR2_SPEED:
      if (btn1Pressed) {
        // Speed UP for Motor 2
        speedIndex2 = (speedIndex2 + 1) % 6;
      }
      else if (btn2Pressed) {
        // Speed DOWN for Motor 2
        speedIndex2 = (speedIndex2 - 1 + 6) % 6;
      }
      else if (btn4Pressed) {
        // BACK to MOTOR2_MODE
        currentState = MOTOR2_MODE;
      }
      break;
  }

  drawInterface();
  delay(50); // Small delay for stability
}

void runMotor(int en, int step, int dir, bool isLocked, int motorSpeedIndex) {
  digitalWrite(en, HIGH); // Wake up motor
  digitalWrite(dir, HIGH);
  
  unsigned long delayTime = speedDelays[motorSpeedIndex];
  
  // Run 200 steps at constant speed
  for(int x = 0; x < 200; x++) {
    digitalWrite(step, HIGH);
    safeDelay(delayTime);
    digitalWrite(step, LOW);
    safeDelay(delayTime);
  }
  
  // Return to locked/unlocked state
  digitalWrite(en, isLocked ? HIGH : LOW);
}
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

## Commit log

2025-07-31 v12 stl
    [v12 - core.stl, v12 - gate 1250x700.stl, v12 - gate 625x352.stl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]
2025-07-31 removed threaded holes
    [v12 - body no threads.stl, v12 - core no threads.stl]
2025-08-01 update core
    [v12 - core.stl, v12 - spool flat.stl]
2026-01-01 v20 STL
    [v20 - core.stl, v20 - gate.stl, v20 - gear center.stl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]
2026-01-24 Create p30t rewinder.stl
    [p30t rewinder.stl]
2026-01-29 add viewfinder
    [v20b - viewfinder part B.stl]
2026-01-29 Update v20b - viewfinder part A.stl
2026-01-30 Create large 35 v1 - main.stl
2026-01-31 film scanner v4
    [scan v4 - base x2.stl, scan v4 - tube.stl]
2026-02-01 fix stl
    [scan v4 - tube.stl]
2026-02-01 scan v5
    [scan v5 - tube 7art35f095+macro16.stl]
2026-02-08 rewinder v2
    [p30t rewinder - v1.stl, p30t rewinder - v2.stl]
2026-02-27 macro tube
    [FD-Lens on Nikon-F macro 17mm.stl, FD-Lens on Nikon-F macro 20mm.stl, FD-Lens on Nikon-F macro 25mm.stl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]
2026-02-27 scan v7
    [scan v7 - holder x2.stl]
